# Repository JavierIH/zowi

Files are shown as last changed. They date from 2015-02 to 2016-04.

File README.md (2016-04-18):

# ZOWI

In this repository you will find the source files for the **bq Zowi** robot. If you are missing something, please do not hesitate to [file an issue on github](https://github.com/bq/zowiissues)

En este repositorio se encuentran los ficheros fuente del robot **Zowi de bq**. Si echas en falta algo, no dudes en [rellenar una tarea en github](https://github.com/bq/zowi/issues)

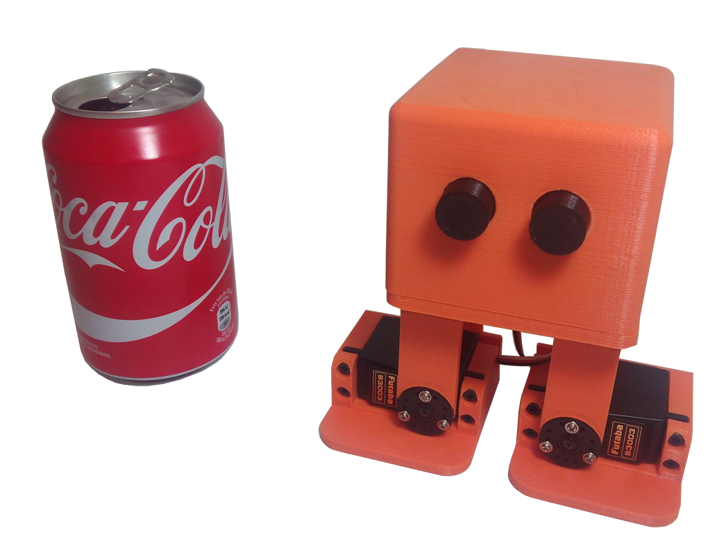
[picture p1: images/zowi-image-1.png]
 

More information in this post in DIWO: [Zowi, introducción a los robots bípedos](http://diwo.bq.com/zowi-introduccion-a-los-robots-bipedos/) (In spanish)

## Designed in Freecad

Zowi is not only an open source robot, but it has also been designed using the open source tool FreeCAD. This way, anyone can open the parts, study them, modify them and distribute the modifications

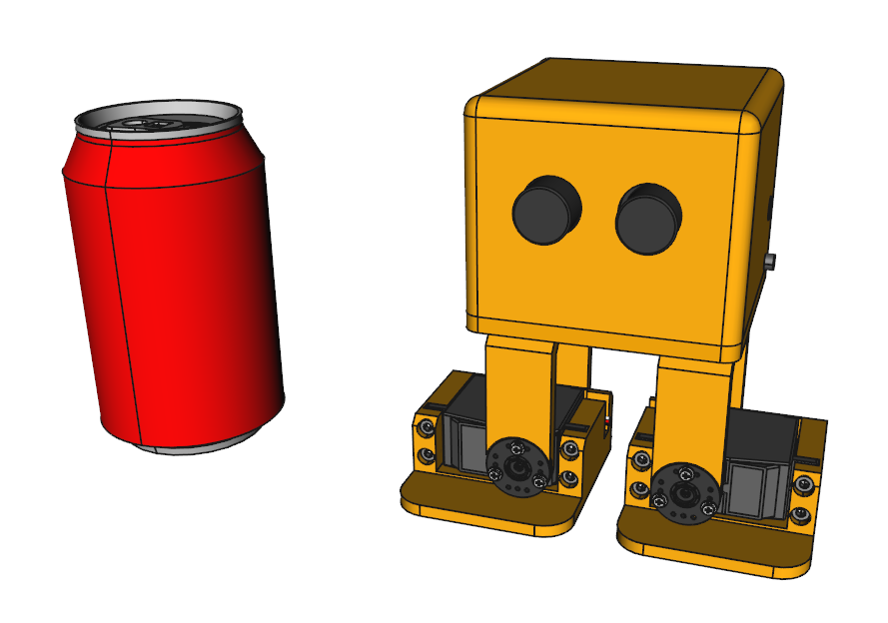
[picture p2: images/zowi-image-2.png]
 

# BOM: Bill of Materials

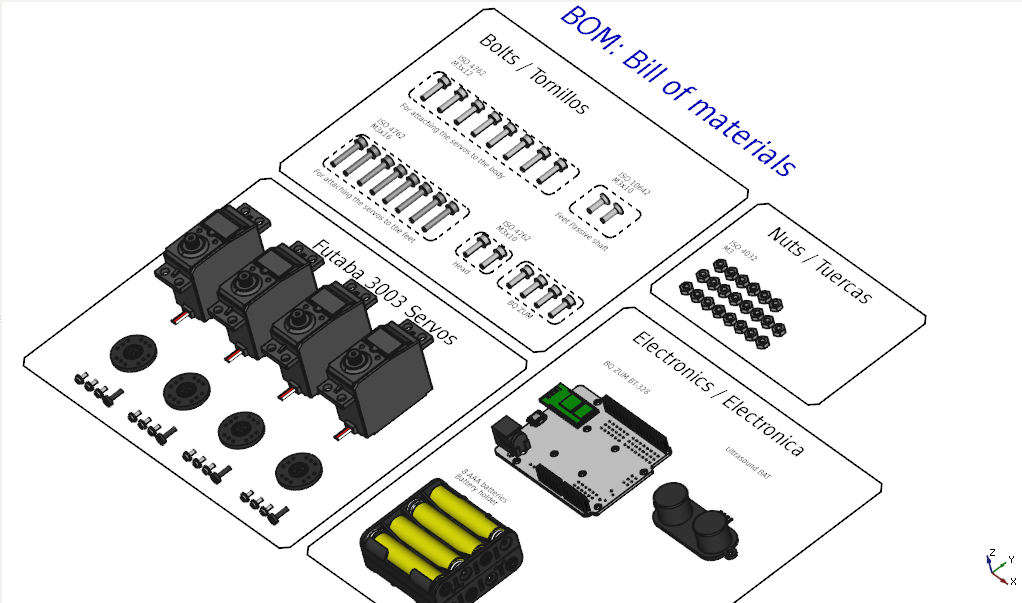
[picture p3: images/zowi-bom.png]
 

* 4 Futaba 3003 servos or compatibles
* 6 M3x10 Bolts (ISO 4762)
* 2 M3x10 Bolts (ISO 10642)
* 8 M3x12 Bolts (ISO 4762)
* 8 M3x16 Bolts (ISO 4762)
* 22 M3 nuts (ISO 4032)
* 1 BQ ZUM BT328 or Arduino
* 4 x 2 AAA Battery holder
* 8 AAA bateries

# License 



This robot is licensed under a [Creative Commons Attribution-ShareAlike 4.0 International License](http://creativecommons.org/licenses/by-sa/4.0/). Please read the LICENSE files for more details.

Este robot tiene una licencia [Creative Commons Attribution-ShareAlike 4.0 International License](http://creativecommons.org/licenses/by-sa/4.0/). Por favor, lea los ficheros LICENSE para más detalles

Original concept by [k120189](http://www.thingiverse.com/k120189/about) on [Thingiverse](http://www.thingiverse.com/thing:43708)

More information: [Zowi CC-BY-SA](http://diwo.bq.com/zowi-cc-by-sa/)

# Other

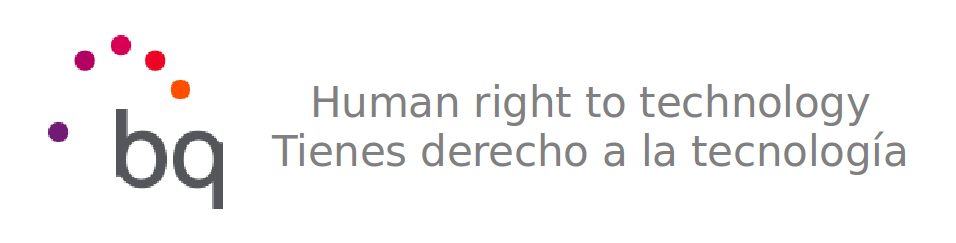
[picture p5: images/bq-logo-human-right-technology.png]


Sponsored by BQ till march 2016

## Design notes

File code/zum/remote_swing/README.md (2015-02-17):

accController -> Protocoder
swing -> Zum (Arduino)

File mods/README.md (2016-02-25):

#Zowi mods

| JIM | Scopum | Micro Raider |
| --- | --- | --- | --- |
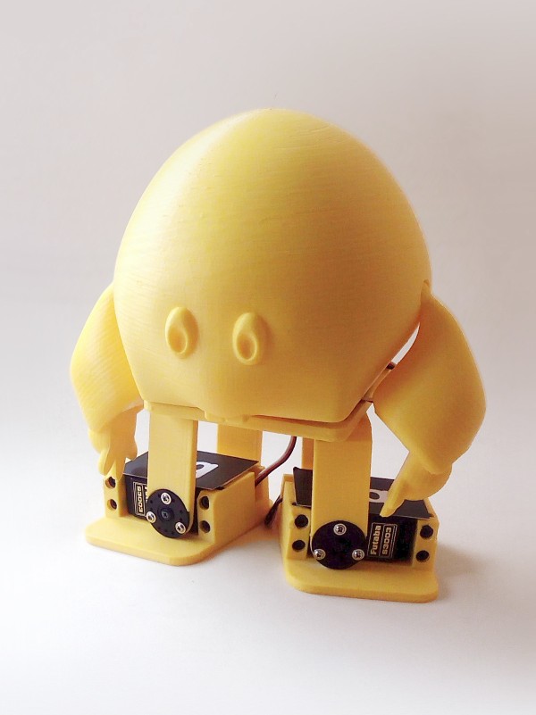
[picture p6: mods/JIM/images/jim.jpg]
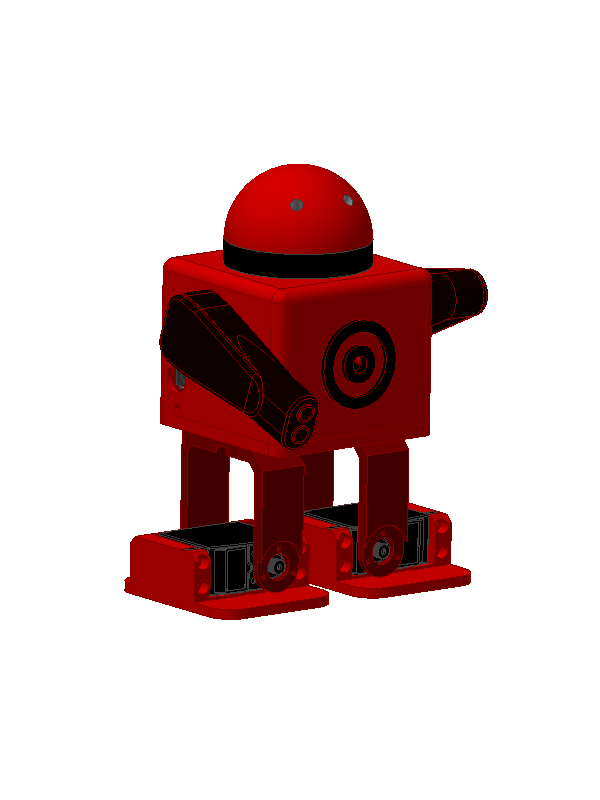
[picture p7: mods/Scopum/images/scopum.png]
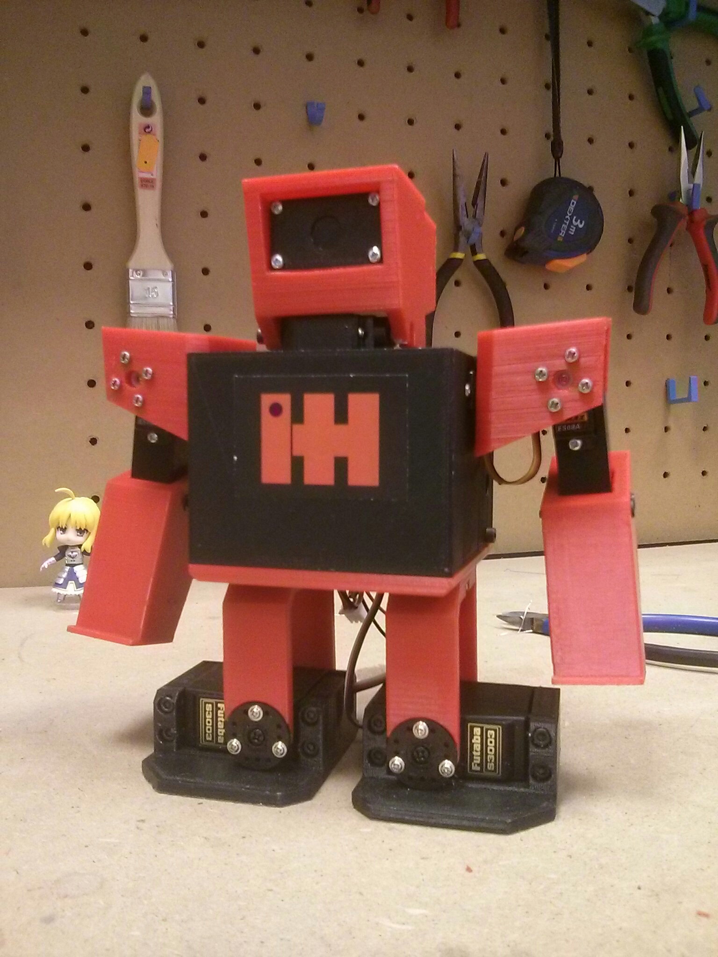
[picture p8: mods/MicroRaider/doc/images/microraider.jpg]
|  |  |  |
| By [Sonia Verdú](http://www.soniaverdu.es/) | By [Macarena González](https://github.com/MacarenaGB)| By  [Javier Isabel](https://github.com/JavierIH)|

| Forge | Zowiquilator | Kobuki |
| --- | --- | --- | --- |
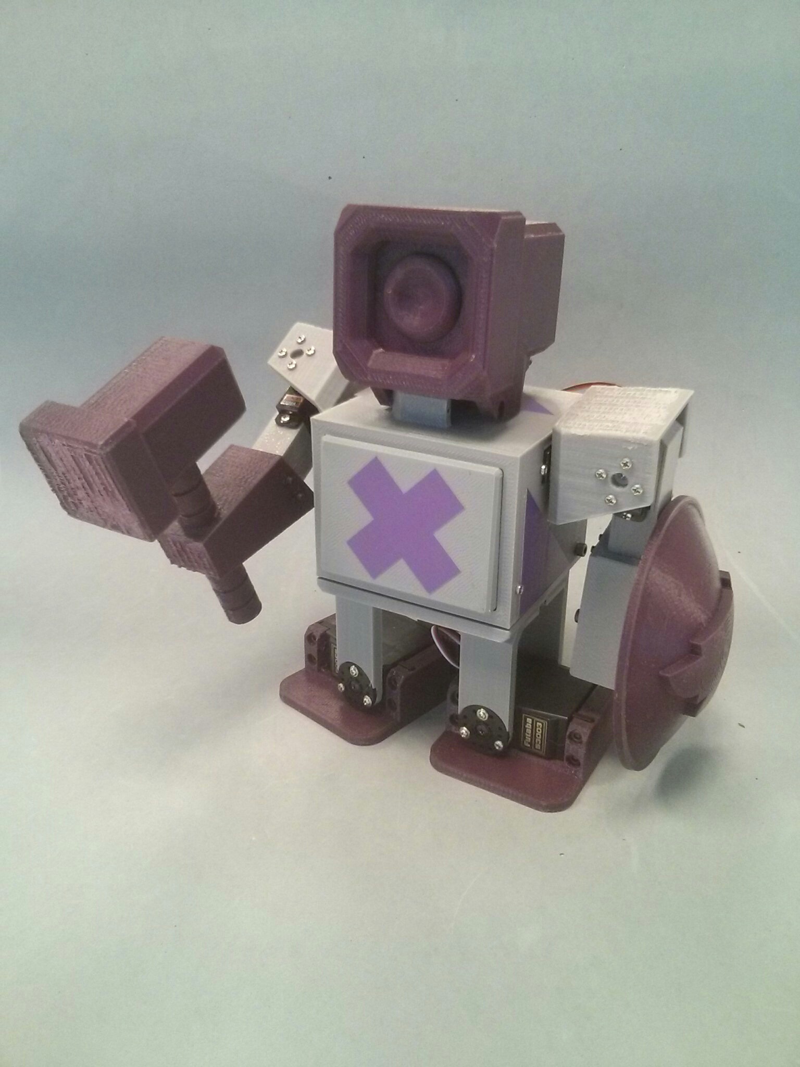
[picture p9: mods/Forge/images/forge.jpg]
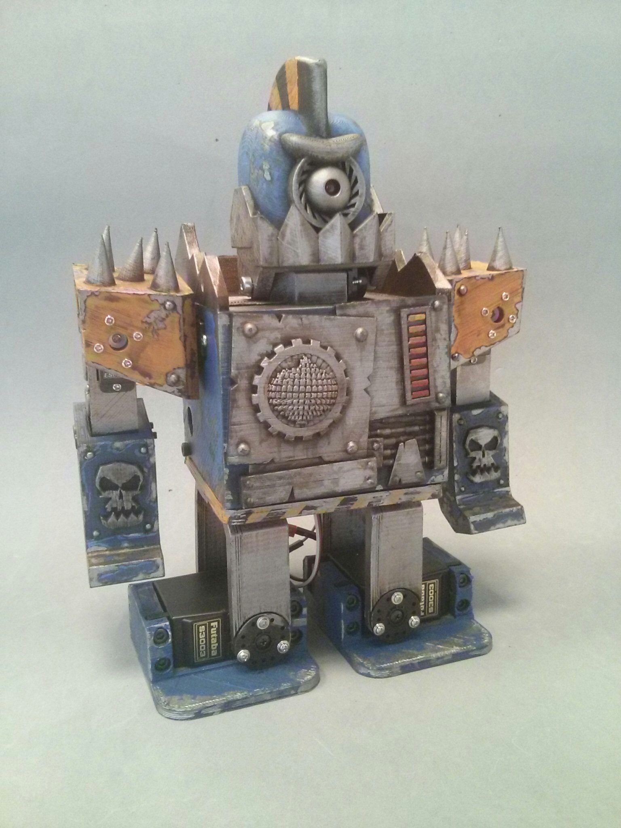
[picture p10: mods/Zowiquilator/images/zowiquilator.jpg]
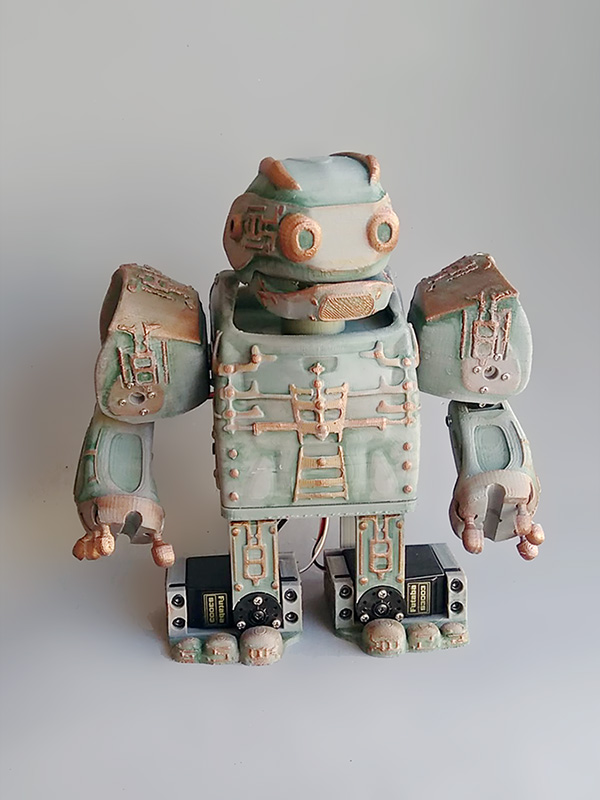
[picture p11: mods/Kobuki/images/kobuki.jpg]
| |  |  |
| By [David Sánchez](https://github.com/davidsanfal) | by [Alberto Arribas](http://www.albertoarribasart.com/)  | By [Sonia Verdú](http://www.soniaverdu.es/) |

| Zowimanoid (template)| IronZowi |  |
| --- | --- | --- | --- |
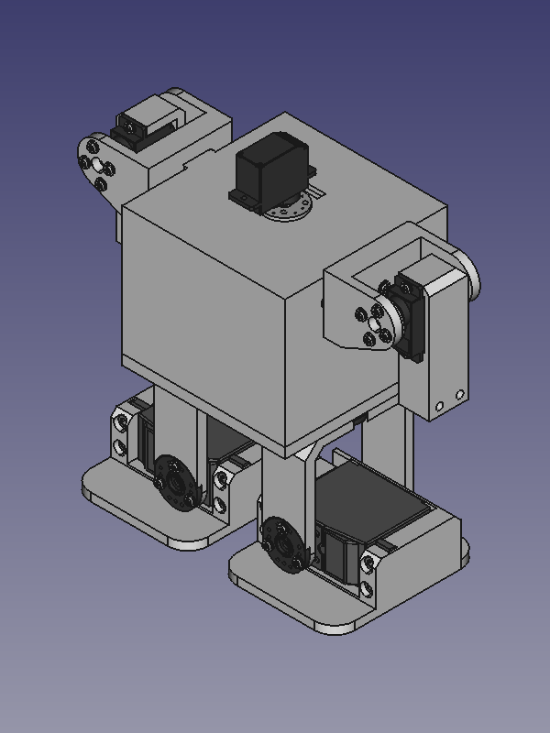
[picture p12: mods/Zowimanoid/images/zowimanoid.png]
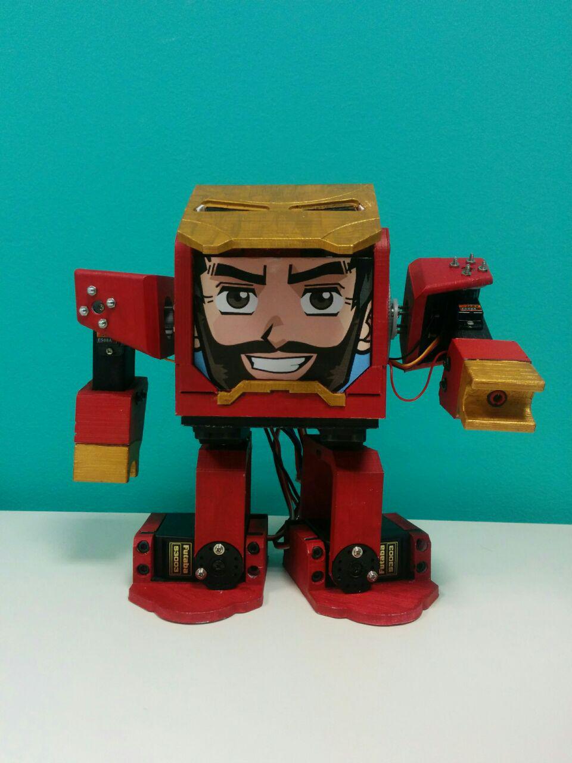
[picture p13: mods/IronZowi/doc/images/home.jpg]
|  | | |
| By  [Javier Isabel](https://github.com/JavierIH) | By  [Gianluca Pugliese](https://github.com/owenlab) | |

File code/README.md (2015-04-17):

La librería de osciladores utilizada en estos programas, puede descargarse desde https://github.com/Obijuan/ArduSnake

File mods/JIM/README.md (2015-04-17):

<p align="center">

</p>
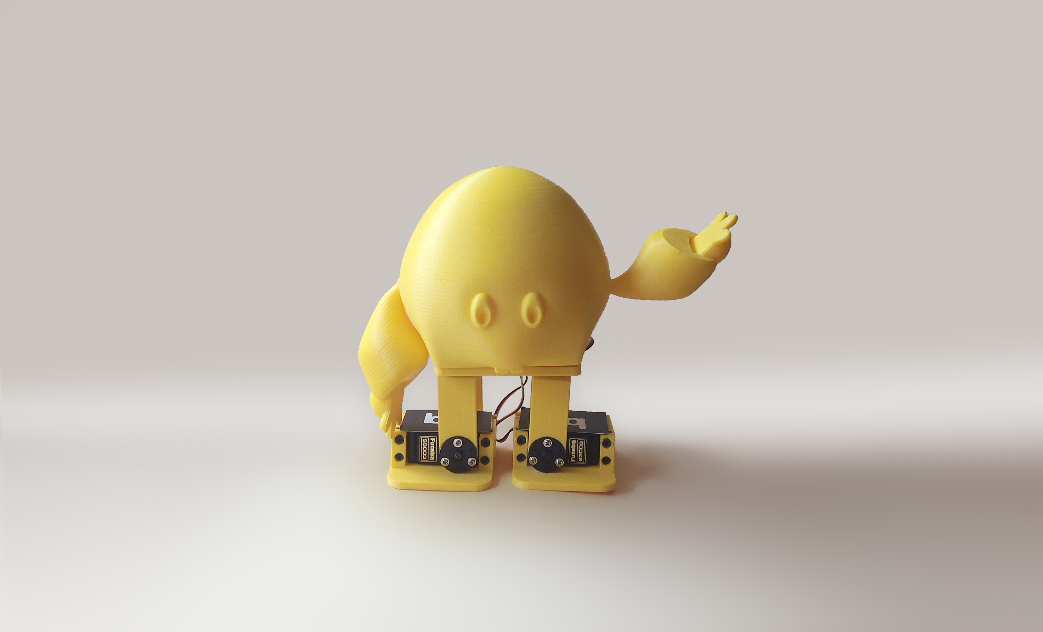
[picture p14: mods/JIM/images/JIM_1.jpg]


# License 



This robot is licensed under a [Creative Commons Attribution-ShareAlike 4.0 International License](http://creativecommons.org/licenses/by-sa/4.0/). Please read the LICENSE files for more details.

Este robot tiene la licencia [Creative Commons Attribution-ShareAlike 4.0 International License](http://creativecommons.org/licenses/by-sa/4.0/). Por favor, lea los ficheros LICENSE para más detalles

# CREDITS

* **Sonia Verdú Calatayud**: Original design

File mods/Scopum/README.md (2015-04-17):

# Scopum

Scopum has been created by [HackLab UPM Bq](http://hacklabupm.bq.com/doku.php?id=start). 
He has been designed in order to have a battle with more Scopums. He has a target in the chest with a receptor fototransistor and a emisor diode in the weapon which is in his arm. Besides, he include a buzzer destinated to make sound when he shoots and when he dies.

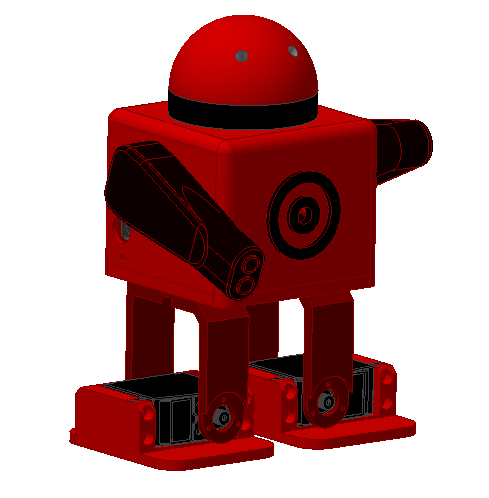
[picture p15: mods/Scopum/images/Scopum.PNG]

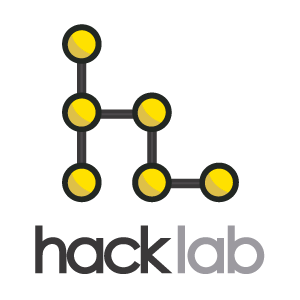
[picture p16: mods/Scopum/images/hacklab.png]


Original concept by [JavierIH](https://github.com/JavierIH) on [Github](https://github.com/bq/zowi)

# License 



This robot is licensed under a [Creative Commons Attribution-ShareAlike 4.0 International License](http://creativecommons.org/licenses/by-sa/4.0/). Please read the LICENSE files for more details.

Este robot tiene la licencia [Creative Commons Attribution-ShareAlike 4.0 International License](http://creativecommons.org/licenses/by-sa/4.0/). Por favor, lea los ficheros LICENSE para más detalles

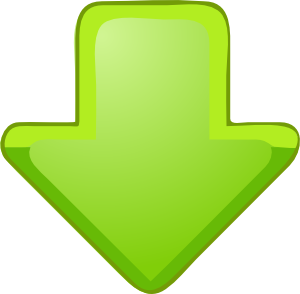
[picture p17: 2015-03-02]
code/protocoder/images/arrow-down-300px.png

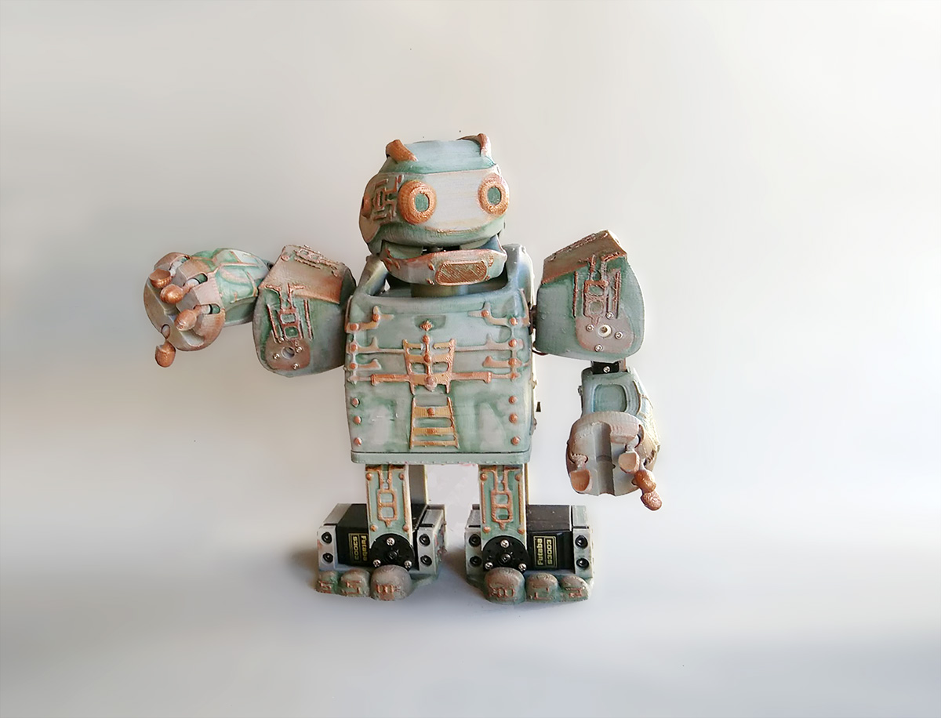
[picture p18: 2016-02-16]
mods/Kobuki/images/kobuki 02.jpg

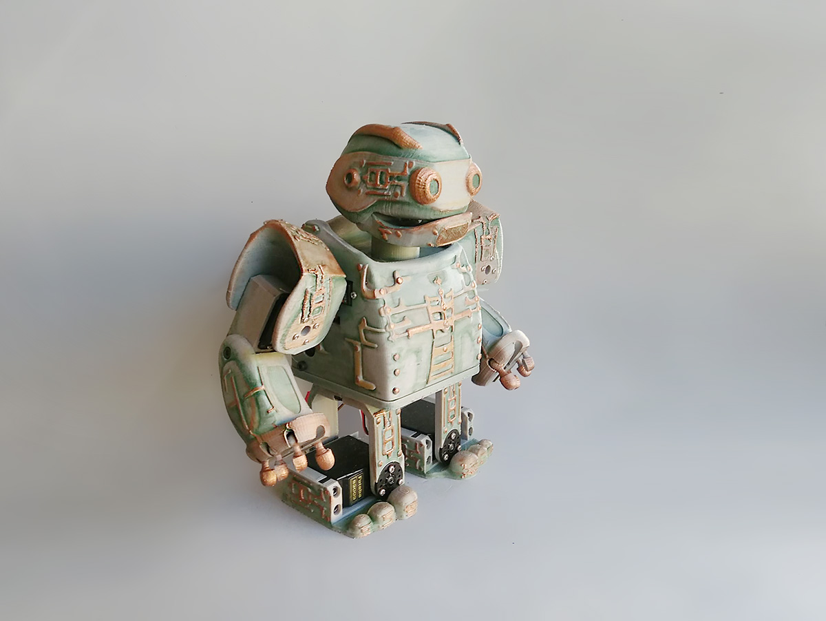
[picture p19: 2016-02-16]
mods/Kobuki/images/kobuki 03.jpg

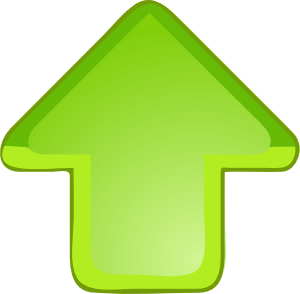
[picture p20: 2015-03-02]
code/protocoder/images/arrow-up.png

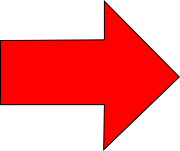
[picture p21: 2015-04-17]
mods/Scopum/code/Protocoder/images/mover_derecha.png

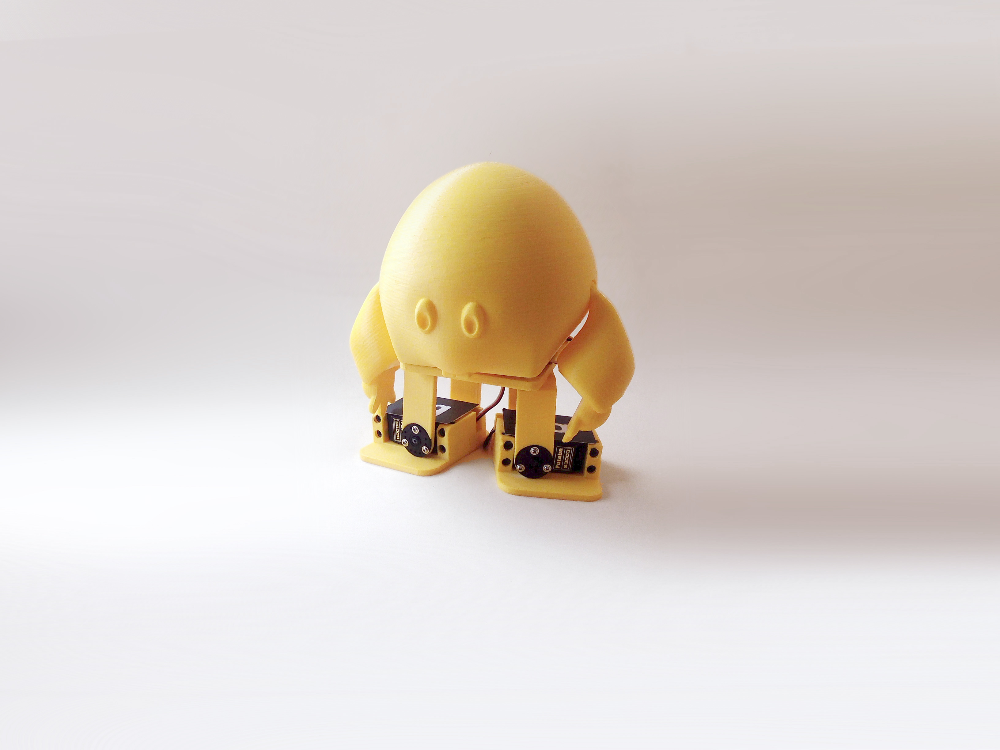
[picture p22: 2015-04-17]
mods/JIM/images/JIM_2.jpg

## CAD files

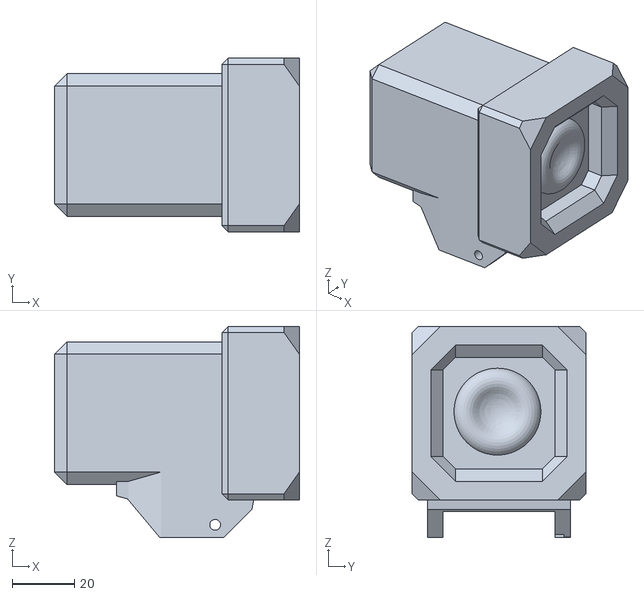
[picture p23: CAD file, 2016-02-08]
mods/Forge/parts/stl/head.stl
79.0 x 56.0 x 68.1

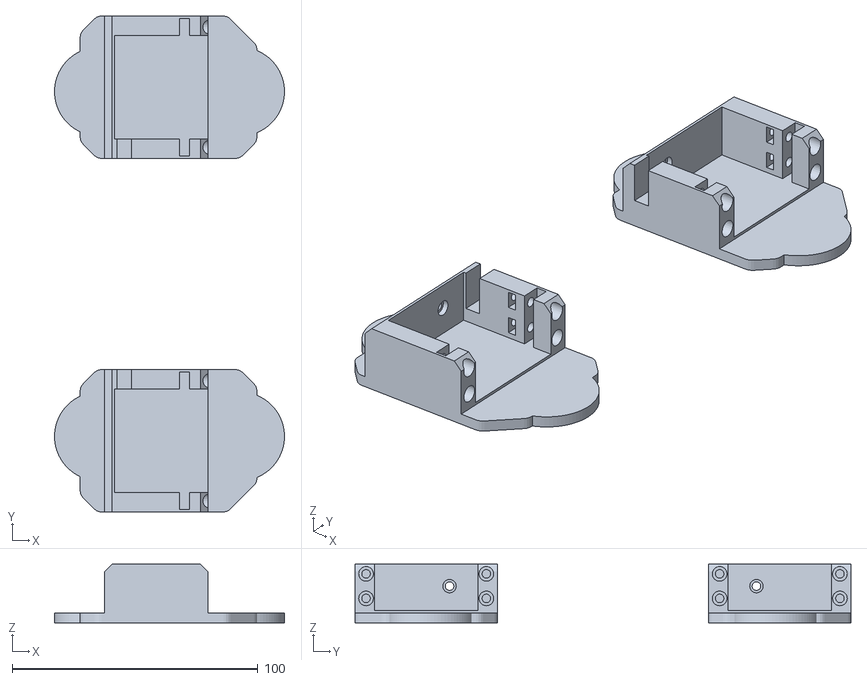
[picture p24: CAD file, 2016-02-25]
mods/IronZowi/parts/stl/feet.stl
93.7 x 202.0 x 24.0

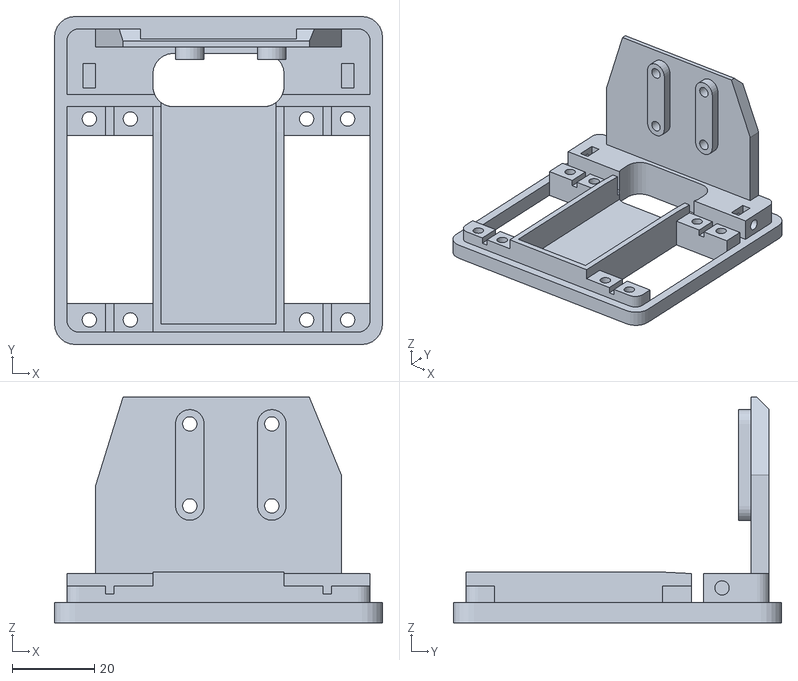
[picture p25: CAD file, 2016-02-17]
mods/Kobuki/parts/stl/base.stl
80.0 x 80.0 x 55.0

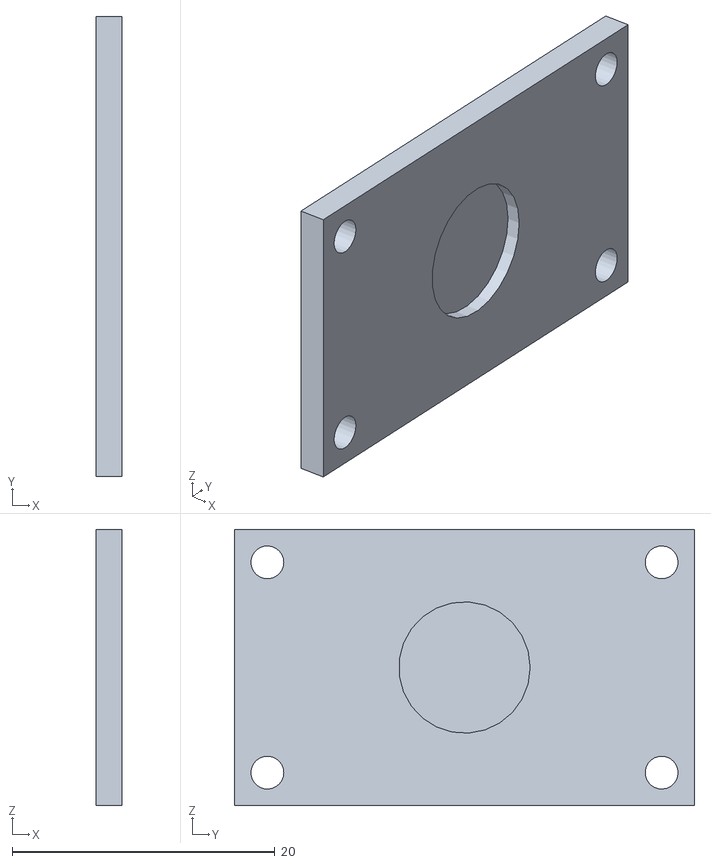
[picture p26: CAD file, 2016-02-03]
mods/MicroRaider/parts/stl/face.stl
2.00 x 35.0 x 21.0

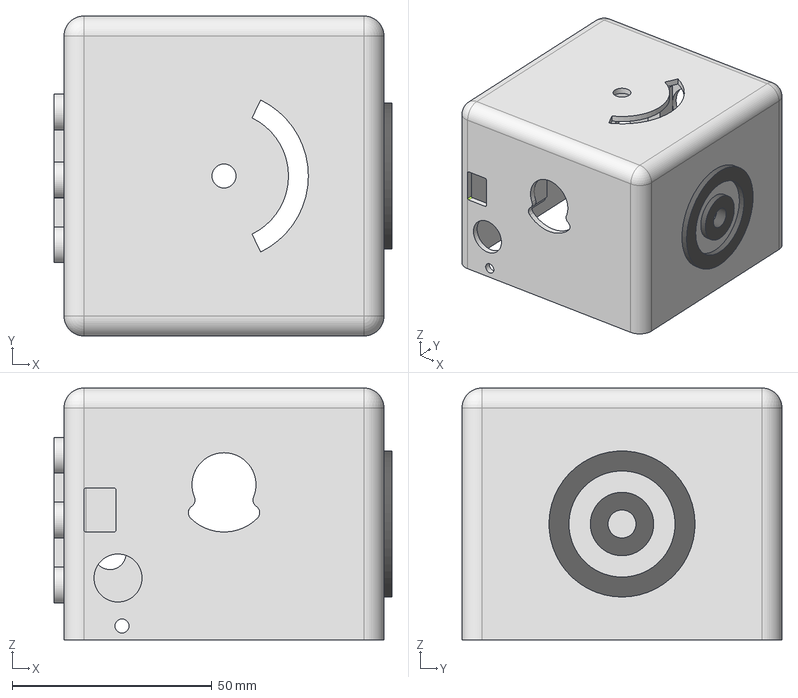
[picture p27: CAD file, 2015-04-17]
mods/Scopum/parts/step/body.step
84.5 x 80.0 x 63.0 mm

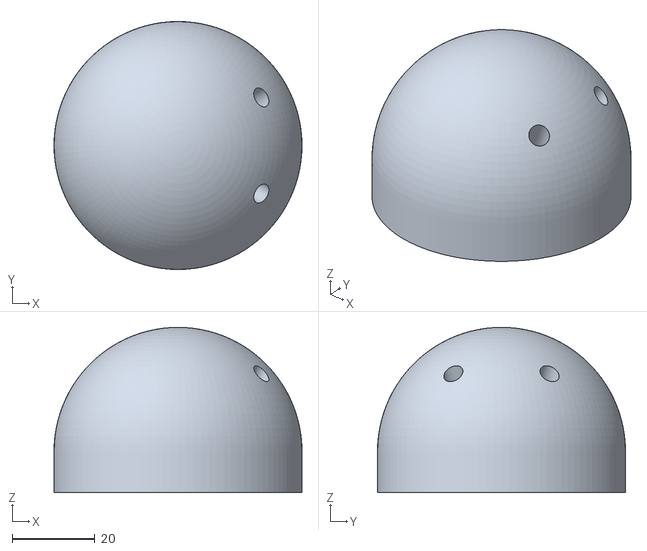
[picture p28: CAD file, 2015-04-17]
mods/Scopum/parts/stl/head.stl
60.0 x 60.0 x 40.0

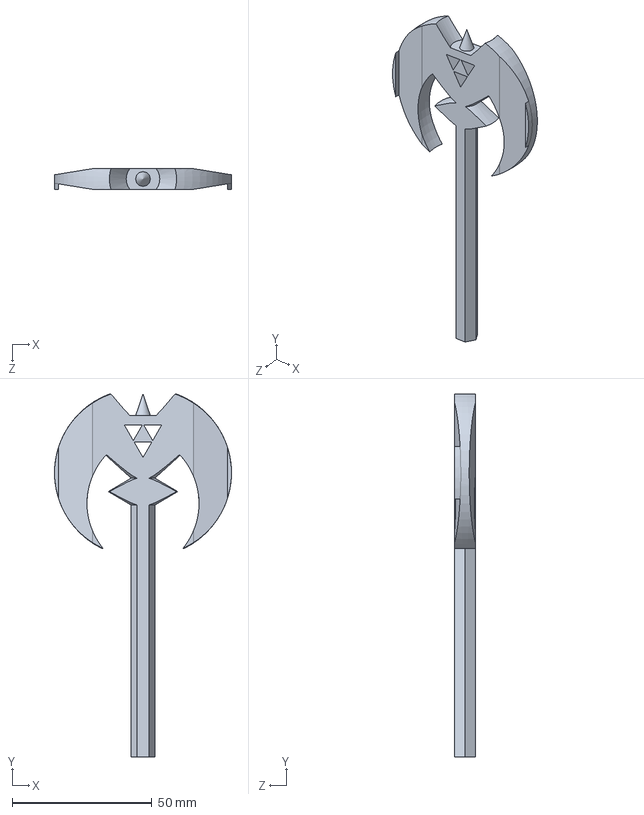
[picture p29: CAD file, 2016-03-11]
mods/Zowarrior/parts/solid/axe.SLDPRT
63.2 x 129.6 x 7.40 mm

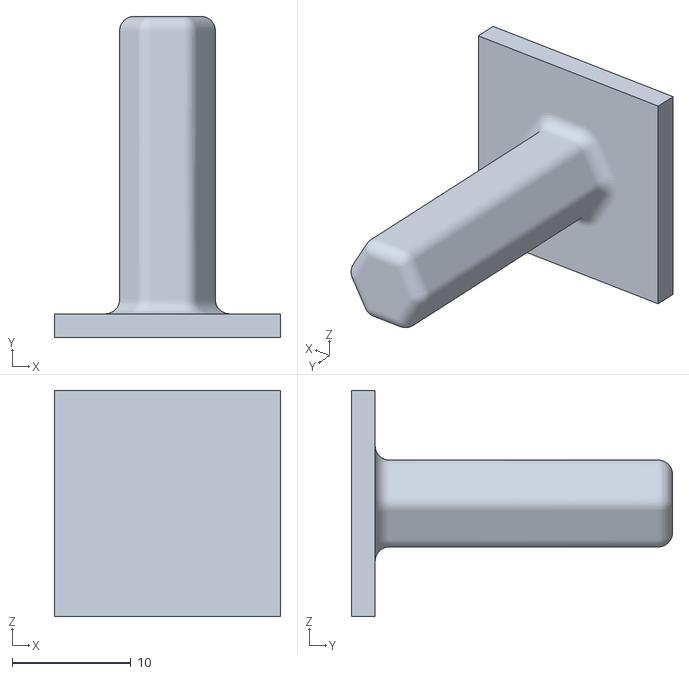
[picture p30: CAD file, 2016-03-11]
mods/Zowarrior/parts/stl/shield_hand.STL
19.0 x 27.0 x 19.0

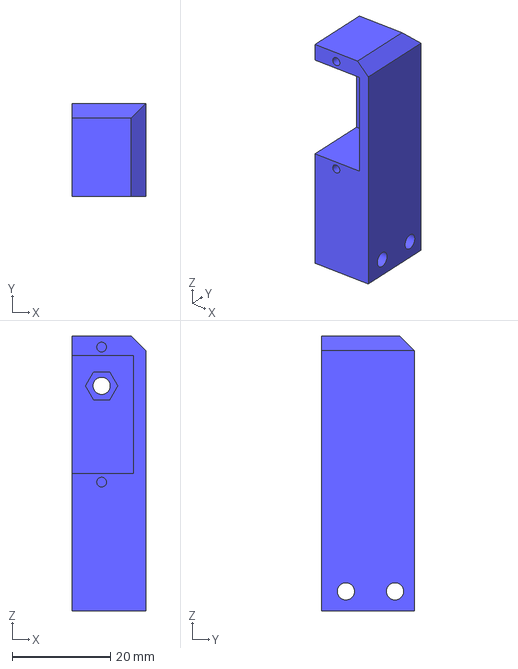
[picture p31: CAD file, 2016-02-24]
mods/Zowimanoid/parts/step/leftArm.step
15.0 x 19.0 x 56.0 mm

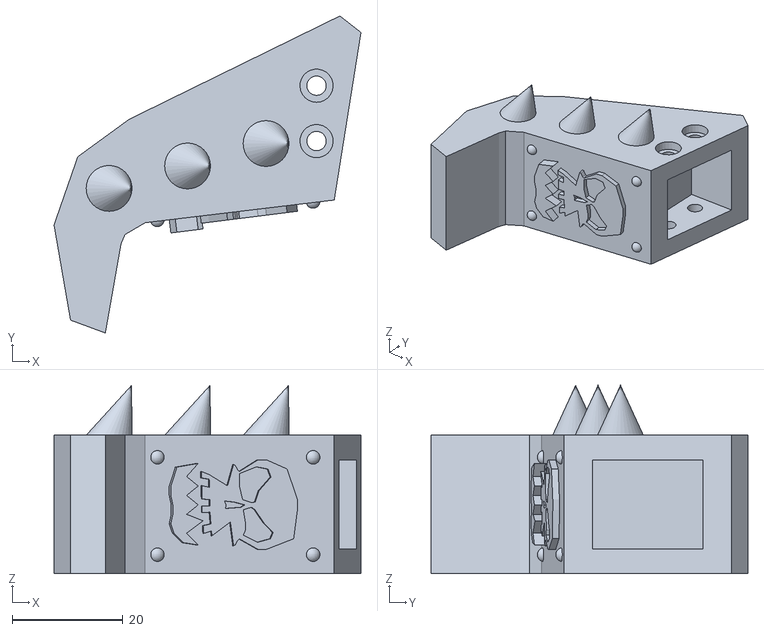
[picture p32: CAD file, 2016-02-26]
mods/Zowiquilator/parts/stl/PunoD_fixed.stl
55.4 x 57.3 x 34.0

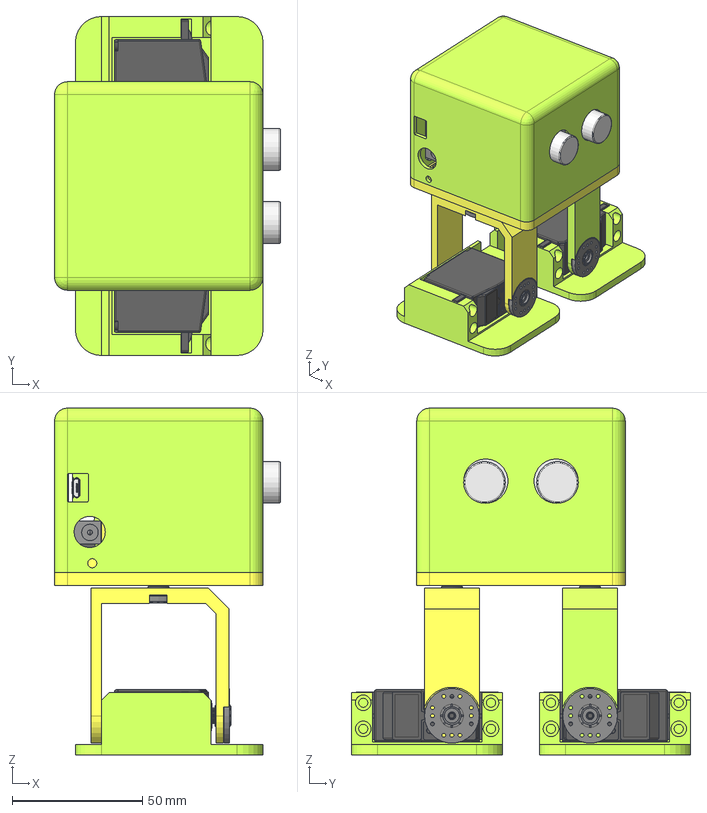
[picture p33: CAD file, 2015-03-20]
parts/freecad/zob.fcstd
86.7 x 130.0 x 133.0 mm
J1
J2
J4
J16
PCB
J010
U1
J8
Servo-D1
Servo-D2
Servo-D1 (Mirror #1)
Servo-D2 (Mirror #2)
horn
horn001
horn (Mirror #4)
horn001 (Mirror #5)
pies001
pies
pataD
pataI
peterpilas
Ultrasonido_BAT
chasis

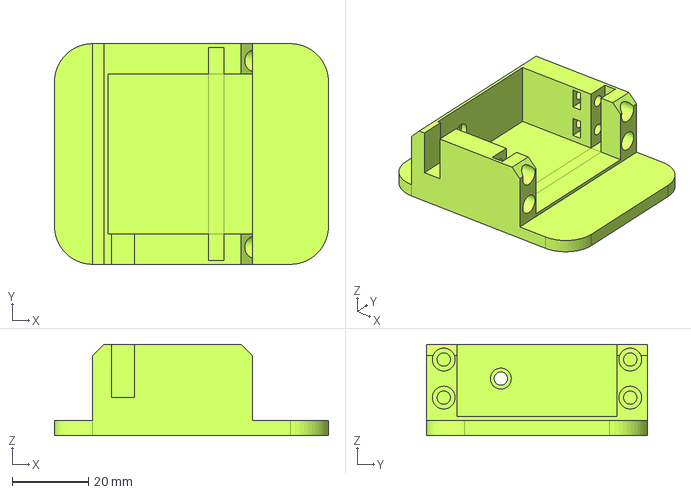
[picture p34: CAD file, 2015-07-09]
parts/step/footL.step
72.0 x 58.0 x 24.0 mm

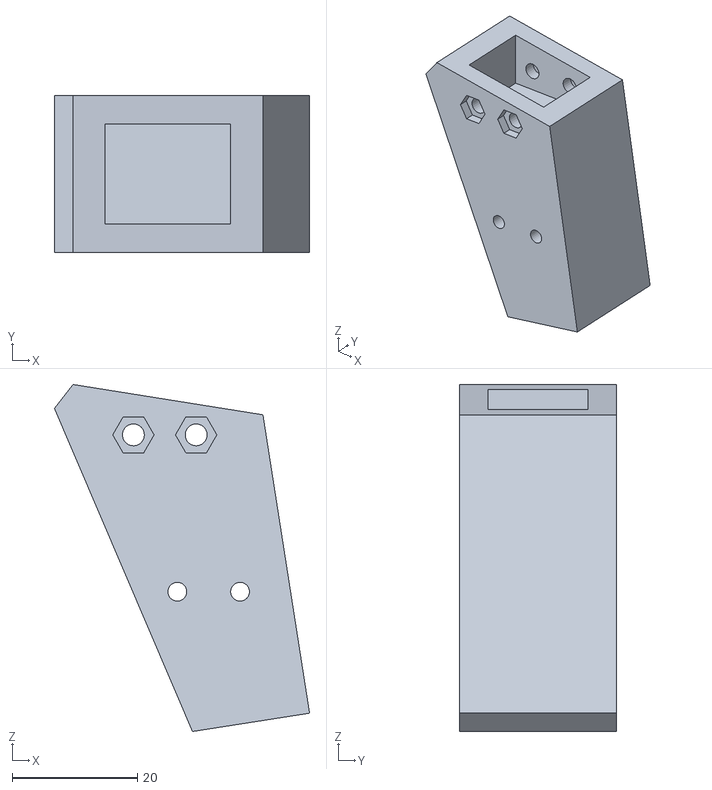
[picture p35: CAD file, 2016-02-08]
mods/Forge/parts/stl/handL.stl
40.7 x 25.0 x 55.3

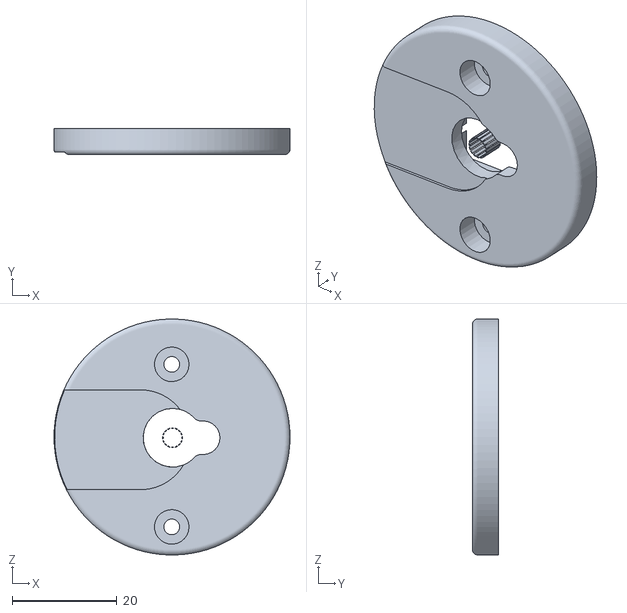
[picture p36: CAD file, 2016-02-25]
mods/IronZowi/parts/stl/ear2.stl
45.0 x 5.00 x 45.0

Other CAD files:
mods/Kobuki/parts/stl/jaw.stl
mods/MicroRaider/parts/stl/faceB.stl
mods/Scopum/parts/step/chassis.step
mods/Scopum/parts/stl/ZUM_BT_328.stl
mods/Forge/parts/stl/armL.stl
mods/Forge/parts/stl/armR.stl
mods/Forge/parts/stl/body.stl
mods/Forge/parts/stl/body_button.stl
mods/Forge/parts/stl/chassis.stl
mods/Forge/parts/stl/footL.stl
mods/Forge/parts/stl/footR.stl
mods/Forge/parts/stl/handR.stl
mods/Forge/parts/stl/leg.stl
mods/Forge/parts/stl/shield.stl
mods/Forge/parts/stl/shoulderL.stl
mods/Forge/parts/stl/shoulderR.stl
mods/IronZowi/parts/stl/arms.stl
mods/IronZowi/parts/stl/base.stl
mods/IronZowi/parts/stl/ear1.stl
mods/IronZowi/parts/stl/hands.stl
mods/IronZowi/parts/stl/head.stl
mods/IronZowi/parts/stl/mask.stl
mods/IronZowi/parts/stl/shoulders.stl
mods/IronZowi/parts/stl/top.stl
mods/Kobuki/parts/stl/head.stl
mods/Kobuki/parts/stl/humerus right.stl
mods/Kobuki/parts/stl/left foot.stl
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

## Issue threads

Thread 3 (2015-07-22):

Refactorization of zowi parts

Obijuan, 2015-07-22:
Zowi parts can be implemented easily using sketches and clones. It will make it easier for the people to change the parts and create derivative designs.

Obijuan, 2015-07-22:
The leg part has been already refactored. I am working in my fork. When every part is finished, printed and tested I will merge into zowi's master

Leg parts has not been printed nor tested yet

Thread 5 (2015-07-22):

[Improvement] Improve how the Futaba 3003 fits in the foot

Obijuan, 2015-07-22:
The Futaba 3003 servo does not fit well on the foot. It have to be pressed hard. It is also difficult to remove.  It would be better improve this part, so that the servos can be attached and detached easily

cparrapa, 2016-02-14:
Had same issue also the pin in the back limit the use of one kind of m3 screw.

arodriguezf, 2016-03-11:
I had the same problem

jabyrd3, 2017-12-09:
I had to file down a small fin on the plastic support tabs to get the futaba servo to fit at all. Pressing hard didn't even do the trick.

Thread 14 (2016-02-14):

Como evadir obstaculos con Zowi?

cparrapa, 2016-02-14:
Hola de antemano gracias por los modelos 3d y las librerias para Zowi, pero con ninguno de los códigos en podido hacer que Zowi evada obstáculos con el ultrasonido, alguna sugerencia?

cparrapa, 2016-02-19:
Any quick code to make Zowi avoid obstacles?

Anadeprado, 2016-02-19:
Debes tener tu sensorUS conectado a pines:  _trigger_pin_, _echo_pin_

Dentro del bucle principal, podrías medir distancia cada vez que Zowi de un pasito:
```
   zowi.walk(1,1000,1);                  //Zowi da un paso

   int distance = getDistance();         //Medimos distancia

        if(distance<15){                 //Si hay algo a 15 centímetros...
                //...Obstacle Detected
        }else{
                //...No Obstacle
        }

```

Funciones para medir distancia en centímetros con el sensorUS:

```
long TP_init(){

  digitalWrite(trigger_pin, LOW);
  delayMicroseconds(2);
  digitalWrite(trigger_pin, HIGH);
  delayMicroseconds(10);
  digitalWrite(trigger_pin, LOW);
  long microseconds = pulseIn(echo_pin ,HIGH,40000);
  return microseconds;

}

long getDistance(){

     long microseconds = TP_init();
     long distance;
     distance = microseconds/29/2;
     if (distance == 0){
             distance = 999;
     }
     return distance;
}
```

cparrapa, 2016-02-20:
@Anadeprado funciono!, mil gracias, luego de una semana intentando era así de simple, al parecer las librerías de aquí** bq / zowiLibs** no funcionan con los mismos códigos que las de este repositorio (**bqlabs/zowi**); en uno llaman Zowi zowi y en otro z, y el zowi.h es diferente, y la final para que funcionara tuve que utilizar el setup de **bq/bitbloqLibs** como en un tutorial de @agomezgar, el código final fue el siguiente:
```
#include <BitbloqZowi.h>
#include <BitbloqUS.h>
#include <BitbloqBatteryReader.h>
#include <BitbloqLedMatrix.h>
#include <Servo.h>
#include <BitbloqOscillator.h>
#include <EEPROM.h>
#define PIN_RR 5
#define PIN_RL 4
#define PIN_YR 3
#define PIN_YL 2
#define trigger_pin 8
#define echo_pin 9
#define TRIM_RR   0
#define TRIM_RL   -5
#define TRIM_YR   0
#define TRIM_YL  -5

Zowi zowi;
void setup()
{
  zowi.init();
    zowi.init(PIN_YL, PIN_YR, PIN_RL, PIN_RR);
    zowi.setTrims(TRIM_YL, TRIM_YR, TRIM_RL, TRIM_RR);
}
void loop()
{
  zowi.home();
  zowi.sing(S_happy);
           zowi.walk(1,1000,1);         //Zowi da un paso

   int distance = getDistance();         //Medimos distancia
        if(distance<15){                 //Si hay algo a 15 centímetros...
              zowi.walk(4, LOW_SPEED, BACKWARD);  //...Obstacle Detected
    zowi.sing(S_confused);
      }else{
                 //...No Obstacle
        }
}
long TP_init(){
  digitalWrite(trigger_pin, LOW);
  delayMicroseconds(2);
  digitalWrite(trigger_pin, HIGH);
  delayMicroseconds(10);
  digitalWrite(trigger_pin, LOW);
  long microseconds = pulseIn(echo_pin ,HIGH,40000);
  return microseconds;
}

long getDistance(){
     long microseconds = TP_init();
     long distance;
     distance = microseconds/29/2;
     if (distance == 0){
             distance = 999;
     }
     return distance;
}
```

Closed 2016-02-20.

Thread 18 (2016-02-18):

Zowimaoid neutral CAD files please

cparrapa, 2016-02-18:
Hi @JavierIH can you please provide .stp or .igs neutral CAD files so i can work on top of that in other 3d software aside from freeCAD?, zowi/mods/Zowimaoid/

JavierIH, 2016-02-18:
Hi, thank you for your feedback. I have generated steps, obj and stl files. They can be found here: https://github.com/bqlabs/zowi/tree/master/mods/Zowimanoid/parts

cparrapa, 2016-02-19:
Perfect thanks for the quick response.

Closed 2016-02-19.

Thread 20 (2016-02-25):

Puño derecho de Zowiquilator

SummeiL, 2016-02-25:
Hola compañeros,

el puño derecho del mod Zowiquilator creo que es erróneo, podéis subir la pieza correcta? Solo me falta esa para montarlo :)

Gracias!

JavierIH, 2016-02-26:
Hola,
En efecto, el archivo estaba equivocado. Acabo de subir la pieza correcta.

Gracias por el aviso :)

Closed 2016-02-26.

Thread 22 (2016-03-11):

Problem with arduino board

arodriguezf, 2016-03-11:
When I upload the code to an arduino board with a speaker connected to it, it sounds like an constant alarm, sometimes when I reboot the board it starts ok and do the programation, but when I get the alarm it only fires the alarm and don´t do anything. I tested in 2 boards with the same result, can you help me?

cparrapa, 2016-03-14:
Which code and libraries are you using?, double check the connection of the servos. Is it Arduino UNO?

arodriguezf, 2016-03-15:
I'm using the libraries from https://github.com/bq/zowiLibs and code fromhttps://github.com/bq/zowiLibs/tree/master/code%20.ino/ZOWI_BASE_v2 but I think I tried with other codes and I get the same result.
I will check the connection of the servos but they are working when the alarm is not makeing sound.
Yes, is with arduino one.

cparrapa, 2016-03-15:
Try this library https://github.com/bqlabs/zowi/tree/master/code/zum/libraries with this code https://github.com/agomezgar/tutoriales/tree/master/tutorialZowi1/zowi_walk_ino

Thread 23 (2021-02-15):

Problemas compilando

lobras77, 2021-02-15:
Hola. Hace un par de semanas llegó a mis manos una impresora 3d e investigando llegué a Bobwi. He impreso las piezas e iba a montarlo con un Arduino Nano.

He probado todos los códigos de la web de Galileo, el tuyo de Zowi y todos me dan errores en la compilación. Me podrías echar una mano? Te lo agradezco de antemano.

Un saludo

lobras77, 2021-02-15:
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
Esto es lo que me sale al copiar y pegar el código y compilarlo.

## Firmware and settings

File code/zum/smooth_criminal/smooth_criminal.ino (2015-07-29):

#include <Servo.h>
#include <Oscillator.h>
#include <EEPROM.h>

#define N_SERVOS 4

//-- Have a look at the file zowi_walk_ino.ino for the documentation on how
//-- the servos are attached

#define EEPROM_TRIM 0 //Activar para coger los datos de calibracin desde la memoria interna

#define TRIM_RR -7
#define TRIM_RL -2
#define TRIM_YR  0
#define TRIM_YL -14

#define PIN_RR 5
#define PIN_RL 4
#define PIN_YR 3
#define PIN_YL 2

#define INTERVALTIME 10.0 

Oscillator servo[N_SERVOS];

void goingUp(int tempo);
void drunk (int tempo);
void noGravity(int tempo);
void kickLeft(int tempo);
void kickRight(int tempo);
void run(int steps, int T=500);
void walk(int steps, int T=1000);
void backyard(int steps, int T=3000);
void backyardSlow(int steps, int T=5000);
void turnLeft(int steps, int T=3000);
void turnRight(int steps, int T=3000);
void moonWalkLeft(int steps, int T=1000);
void moonWalkRight(int steps, int T=1000);
void crusaito(int steps, int T=1000);
void swing(int steps, int T=1000);
void upDown(int steps, int T=1000);
void flapping(int steps, int T=1000);

void setup()
{
  Serial.begin(19200);
  
  servo[0].attach(PIN_RR);
  servo[1].attach(PIN_RL);
  servo[2].attach(PIN_YR);
  servo[3].attach(PIN_YL);
  
  //EEPROM.write(0,TRIM_RR);
  //EEPROM.write(1,TRIM_RL);
  //EEPROM.write(2,TRIM_YR);
  //EEPROM.write(3,TRIM_YL);
  
  int trim;
  
  if(EEPROM_TRIM){
    for(int x=0;x<4;x++){
      trim=EEPROM.read(x);
      if(trim>128)trim=trim-256;
      Serial.print("TRIM ");
      Serial.print(x);
      Serial.print(" en ");
      Serial.println(trim);
      servo[x].SetTrim(trim);
    }
  }
  else{
    servo[0].SetTrim(TRIM_RR);
    servo[1].SetTrim(TRIM_RL);
    servo[2].SetTrim(TRIM_YR);
    servo[3].SetTrim(TRIM_YL);
  }
  
  for(int i=0;i<4;i++) servo[i].SetPosition(90);
}

// TEMPO: 121 BPM
int t=495;
double pause=0;

void loop()
{
 // if(Serial.available()){
  //  char init = Serial.read();
   // if (init=='X'){
   //   delay(4000); //3000 - 4500
   
dance();


//for(int i=0;i<4;i++) servo[i].SetPosition(90);

      
          for(int i=0;i<4;i++) servo[i].SetPosition(90);
   // }
 // }
}

void dance(){
  primera_parte();
  segunda_parte();
  moonWalkLeft(4,t*2);
  moonWalkRight(4,t*2);
  moonWalkLeft(4,t*2);
  moonWalkRight(4,t*2);
  primera_parte(); 
  crusaito(1,t*8);
  crusaito(1,t*7);

  for (int i=0; i<16; i++){
    flapping(1,t/4);
    delay(3*t/4);
  }
 
  moonWalkRight(4,t*2);
  moonWalkLeft(4,t*2);
  moonWalkRight(4,t*2);
  moonWalkLeft(4,t*2);

  drunk(t*4);
  drunk(t*4);
  drunk(t*4);
  drunk(t*4);
  kickLeft(t);
  kickRight(t);
  drunk(t*8);
  drunk(t*4);
  drunk(t/2);
  delay(t*4); 

  drunk(t/2);

  delay(t*4); 
  walk(2,t*2);
  backyard(2,t*2);
  goingUp(t*2);
  goingUp(t*1);
  noGravity(t*2);
  crusaito(1,t*2);
  crusaito(1,t*8);
  crusaito(1,t*2);
  crusaito(1,t*8);
  crusaito(1,t*2);
  crusaito(1,t*3);

  delay(t);
  primera_parte();
    for (int i=0; i<32; i++){
    flapping(1,t/2);
    delay(t/2);
  }
  
  for(int i=0;i<4;i++) servo[i].SetPosition(90);
}




////////////////////////////////////////////////////////////////////////////////////////
//////////////////////////////////FUNCIONES DE CONTROL//////////////////////////////////
////////////////////////////////////////////////////////////////////////////////////////

void oscillate(int A[N_SERVOS], int O[N_SERVOS], int T, double phase_diff[N_SERVOS]){
  for (int i=0; i<4; i++) {
    servo[i].SetO(O[i]);
    servo[i].SetA(A[i]);
    servo[i].SetT(T);
    servo[i].SetPh(phase_diff[i]);
  }
  double ref=millis();
   for (double x=ref; x<T+ref; x=millis()){
     for (int i=0; i<4; i++){
        servo[i].refresh();
     }
  }
}

unsigned long final_time;
unsigned long interval_time;
int oneTime;
int iteration;
float increment[N_SERVOS]; 
int oldPosition[]={90,90,90,90};

void moveNServos(int time, int  newPosition[]){
  for(int i=0;i<N_SERVOS;i++)	increment[i] = ((newPosition[i])-oldPosition[i])/(time/INTERVALTIME);
  
  final_time =  millis() + time; 
  
  iteration = 1; 
  while(millis() < final_time){ //Javi del futuro cambia esto  
      interval_time = millis()+INTERVALTIME;  
      
      oneTime=0;      
      while(millis()<interval_time){	  
          if(oneTime<1){ 
              for(int i=0;i<N_SERVOS;i++){
                  servo[i].SetPosition(oldPosition[i] + (iteration * increment[i]));
              }			
              iteration++;
              oneTime++;
          }
      }     
  }   

  for(int i=0;i<N_SERVOS;i++){	
    oldPosition[i] = newPosition[i];
  }   
}


//////////////////////////////////////////////////////////////////////////////
////////////////////////////////PASOS DE BAILE////////////////////////////////
//////////////////////////////////////////////////////////////////////////////

void goingUp(int tempo){
  
      pause=millis();
      for(int i=0;i<4;i++) servo[i].SetPosition(90);
      delay(tempo);
      servo[0].SetPosition(80);
      servo[1].SetPosition(100);
      delay(tempo);
      servo[0].SetPosition(70);
      servo[1].SetPosition(110);
      delay(tempo);
      servo[0].SetPosition(60);
      servo[1].SetPosition(120);
      delay(tempo);
      servo[0].SetPosition(50);
      servo[1].SetPosition(130);
      delay(tempo);
      servo[0].SetPosition(40);
      servo[1].SetPosition(140);
      delay(tempo);
      servo[0].SetPosition(30);
      servo[1].SetPosition(150);
      delay(tempo);
      servo[0].SetPosition(20);
      servo[1].SetPosition(160);
      delay(tempo);
      
      while(millis()<pause+8*t);

}

void primera_parte(){
  
  int move1[4] = {60,120,90,90};
  int move2[4] = {90,90,90,90};
  int move3[4] = {40,140,90,90};
  
  for(int x=0; x<3; x++){
    for(int i=0; i<3; i++){
      lateral_fuerte(1,t/2);
      lateral_fuerte(0,t/4);
      lateral_fuerte(1,t/4);
      delay(t);
    }
  
    pause=millis();
    for(int i=0;i<4;i++) servo[i].SetPosition(90);
    moveNServos(t*0.4,move1);
    moveNServos(t*0.4,move2);
    while(millis()<(pause+t*2));
  }
  
  for(int i=0; i<2; i++){
    lateral_fuerte(1,t/2);
    lateral_fuerte(0,t/4);
    lateral_fuerte(1,t/4);
    delay(t);
  }
    
  pause=millis();
  for(int i=0;i<4;i++) servo[i].SetPosition(90);
  crusaito(1,t*1.4);
  moveNServos(t*1,move3);
  for(int i=0;i<4;i++) servo[i].SetPosition(90);
  while(millis()<(pause+t*4));
}

void segunda_parte(){
  
  int move1[4] = {90,90,80,100};
  int move2[4] = {90,90,100,80};
  int move3[4] = {90,90,80,100};
  int move4[4] = {90,90,100,80};
    
  int move5[4] = {40,140,80,100};
  int move6[4] = {40,140,100,80};
  int move7[4] = {90,90,80,100};
  int move8[4] = {90,90,100,80};
       
  int move9[4] = {40,140,80,100};
  int move10[4] = {40,140,100,80};
  int move11[4] = {90,90,80,100};
  int move12[4] = {90,90,100,80};
  
  for(int x=0; x<7; x++){ 
    for(int i=0; i<3; i++){
      pause=millis();
      moveNServos(t*0.15,move1);
      moveNServos(t*0.15,move2);
      moveNServos(t*0.15,move3);
      moveNServos(t*0.15,move4);
      while(millis()<(pause+t));
    }
    pause=millis();
    moveNServos(t*0.15,move5);
    moveNServos(t*0.15,move6);
    moveNServos(t*0.15,move7);
    moveNServos(t*0.15,move8);
    while(millis()<(pause+t));
  }
 
  for(int i=0; i<3; i++){
    pause=millis();
    moveNServos(t*0.15,move9);
    moveNServos(t*0.15,move10);
    moveNServos(t*0.15,move11);
    moveNServos(t*0.15,move12);
    while(millis()<(pause+t));
  }
}

void lateral_fuerte(boolean side, int tempo){
  
  for(int i=0;i<4;i++) servo[i].SetPosition(90);
  if (side) servo[0].SetPosition(40);
  else servo[1].SetPosition(140);
  delay(tempo/2);
  servo[0].SetPosition(90);
  servo[1].SetPosition(90);
  delay(tempo/2);

}

void drunk (int tempo){
  
  pause=millis();
  
  int move1[] = {60,70,90,90};
  int move2[] = {110,120,90,90};
  int move3[] = {60,70,90,90};
  int move4[] = {110,120,90,90};
  
  moveNServos(tempo*0.235,move1);
  moveNServos(tempo*0.235,move2);
  moveNServos(tempo*0.235,move3);
  moveNServos(tempo*0.235,move4);
  while(millis()<(pause+tempo));

}


void noGravity(int tempo){
  
  int move1[4] = {120,140,90,90};
  int move2[4] = {140,140,90,90};
  int move3[4] = {120,140,90,90};
  int move4[4] = {90,90,90,90};
  
  
  for(int i=0;i<4;i++) servo[i].SetPosition(90);
  for(int i=0;i<N_SERVOS;i++) oldPosition[i]=90;
  moveNServos(tempo*2,move1);
  moveNServos(tempo*2,move2);
  delay(tempo*2);
  moveNServos(tempo*2,move3);
  moveNServos(tempo*2,move4);

 

}

void kickLeft(int tempo){
  for(int i=0;i<4;i++) servo[i].SetPosition(90);
  delay(tempo);
  servo[0].SetPosition(50); //pie derecho
  servo[1].SetPosition(70); //pie izquiero
  delay(tempo);
  servo[0].SetPosition(80); //pie derecho
  servo[1].SetPosition(70); //pie izquiero
  delay(tempo/4);
  servo[0].SetPosition(30); //pie derecho
  servo[1].SetPosition(70); //pie izquiero
  delay(tempo/4);
  servo[0].SetPosition(80); //pie derecho
  servo[1].SetPosition(70); //pie izquiero
  delay(tempo/4);
  servo[0].SetPosition(30); //pie derecho
  servo[1].SetPosition(70); //pie izquiero
  delay(tempo/4);
  servo[0].SetPosition(80); //pie derecho
  servo[1].SetPosition(70); //pie izquiero
  delay(tempo);
}

void kickRight(int tempo){
for(int i=0;i<4;i++) servo[i].SetPosition(90);
  delay(tempo);
  servo[0].SetPosition(110); //pie derecho
  servo[1].SetPosition(130); //pie izquiero
  delay(tempo);
  servo[0].SetPosition(110); //pie derecho
  servo[1].SetPosition(100); //pie izquiero
  delay(tempo/4);
  servo[0].SetPosition(110); //pie derecho
  servo[1].SetPosition(150); //pie izquiero
  delay(tempo/4);
  servo[0].SetPosition(110); //pie derecho
  servo[1].SetPosition(80); //pie izquiero
  delay(tempo/4);
  servo[0].SetPosition(110); //pie derecho
  servo[1].SetPosition(150); //pie izquiero
  delay(tempo/4);
  servo[0].SetPosition(110); //pie derecho
  servo[1].SetPosition(100); //pie izquiero
  delay(tempo);
}

void walk(int steps, int T){
    int A[4]= {15, 15, 30, 30};
    int O[4] = {0, 0, 0, 0};
    double phase_diff[4] = {DEG2RAD(0), DEG2RAD(0), DEG2RAD(90), DEG2RAD(90)};
    
    for(int i=0;i<steps;i++)oscillate(A,O, T, phase_diff);
}

void run(int steps, int T){
    int A[4]= {10, 10, 10, 10};
    int O[4] = {0, 0, 0, 0};
    double phase_diff[4] = {DEG2RAD(0), DEG2RAD(0), DEG2RAD(90), DEG2RAD(90)}; 
    
    for(int i=0;i<steps;i++)oscillate(A,O, T, phase_diff);
}

void backyard(int steps, int T){
    int A[4]= {15, 15, 30, 30};
    int O[4] = {0, 0, 0, 0};
    double phase_diff[4] = {DEG2RAD(0), DEG2RAD(0), DEG2RAD(-90), DEG2RAD(-90)}; 
    
    for(int i=0;i<steps;i++)oscillate(A,O, T, phase_diff);
}

void backyardSlow(int steps, int T){
    int A[4]= {15, 15, 30, 30};
    int O[4] = {0, 0, 0, 0};
    double phase_diff[4] = {DEG2RAD(0), DEG2RAD(0), DEG2RAD(-90), DEG2RAD(-90)}; 
    
    for(int i=0;i<steps;i++)oscillate(A,O, T, phase_diff);
}


void turnLeft(int steps, int T){
    int A[4]= {20, 20, 10, 30};
    int O[4] = {0, 0, 0, 0};
    double phase_diff[4] = {DEG2RAD(0), DEG2RAD(0), DEG2RAD(90), DEG2RAD(90)}; 
    
    for(int i=0;i<steps;i++)oscillate(A,O, T, phase_diff);
}

void turnRight(int steps, int T){
    int A[4]= {20, 20, 30, 10};
    int O[4] = {0, 0, 0, 0};
    double phase_diff[4] = {DEG2RAD(0), DEG2RAD(0), DEG2RAD(90), DEG2RAD(90)}; 
    
    for(int i=0;i<steps;i++)oscillate(A,O, T, phase_diff);
}

void moonWalkRight(int steps, int T){
    int A[4]= {25, 25, 0, 0};
    int O[4] = {-15 ,15, 0, 0};
    double phase_diff[4] = {DEG2RAD(0), DEG2RAD(180 + 120), DEG2RAD(90), DEG2RAD(90)}; 
    
    for(int i=0;i<steps;i++)oscillate(A,O, T, phase_diff);
}

void moonWalkLeft(int steps, int T){
    int A[4]= {25, 25, 0, 0};
    int O[4] = {-15, 15, 0, 0};
    double phase_diff[4] = {DEG2RAD(0), DEG2RAD(180 - 120), DEG2RAD(90), DEG2RAD(90)}; 
    
    for(int i=0;i<steps;i++)oscillate(A,O, T, phase_diff);
}

void crusaito(int steps, int T){
    int A[4]= {25, 25, 30, 30};
    int O[4] = {- 15, 15, 0, 0};
    double phase_diff[4] = {DEG2RAD(0), DEG2RAD(180 + 120), DEG2RAD(90), DEG2RAD(90)}; 
    
    for(int i=0;i<steps;i++)oscillate(A,O, T, phase_diff);
}

void swing(int steps, int T){
    int A[4]= {25, 25, 0, 0};
    int O[4] = {-15, 15, 0, 0};
    double phase_diff[4] = {DEG2RAD(0), DEG2RAD(0), DEG2RAD(90), DEG2RAD(90)};
    
    for(int i=0;i<steps;i++)oscillate(A,O, T, phase_diff);
}

void upDown(int steps, int T){
    int A[4]= {25, 25, 0, 0};
    int O[4] = {-15, 15, 0, 0};
    double phase_diff[4] = {DEG2RAD(180), DEG2RAD(0), DEG2RAD(270), DEG2RAD(270)};
    
    for(int i=0;i<steps;i++)oscillate(A,O, T, phase_diff);
}

void flapping(int steps, int T){
    int A[4]= {15, 15, 8, 8};
    int O[4] = {-A[0], A[1], 0, 0};
    double phase_diff[4] = {DEG2RAD(0), DEG2RAD(180), DEG2RAD(90), DEG2RAD(-90)};
    
    for(int i=0;i<steps;i++)oscillate(A,O, T, phase_diff);
}

void test(int steps, int T){
    int A[4]= {15, 15, 8, 8};
    int O[4] = {-A[0] + 10, A[1] - 10, 0, 0};
    double phase_diff[4] = {DEG2RAD(0), DEG2RAD(180), DEG2RAD(90), DEG2RAD(-90)};
    
    for(int i=0;i<steps;i++)oscillate(A,O, T, phase_diff);
}

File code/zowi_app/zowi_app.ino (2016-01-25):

//----------------------------------------------------------------
//-- Zowi basic firmware v2 (Modded for Zowi community edition)
//-- (c) BQ. Released under a GPL licencse
//-- 25 January 2016
//-- Authors:  Javier Isabel:  javier.isabel@bq.com
//--           Anita de Prado: ana.deprado@bq.com
//--           Jose Alberca:   jose.alberca@bq.com
//--           Juan Gonzalez (obijuan): juan.gonzalez@bq.com
//--           Irene Sanz : irene.sanz@bq.com
//-----------------------------------------------------------------
//-- Experiment with all the features that Zowi have!
//-----------------------------------------------------------------

//-- Library to manage external interruptions

//-- Library to manage serial commands
#include <ZowiSerialCommand.h>
ZowiSerialCommand SCmd;  //The SerialCommand object

//-- Zowi Library
#include <Zowi.h>
Zowi zowi;  //This is Zowi!!
 
//---------------------------------------------------------
//-- Configuration of pins where the servos are attached
/*
         --------------- 
        |               |
        |     O   O     |
        |               |
 YR ==> |               | <== YL
         --------------- 
            ||     ||
            ||     ||
            ||     ||
 RR ==>  ------   ------  <== RL
         ------   ------
*/

  #define PIN_YL 2 //servo[0]
  #define PIN_YR 3 //servo[1]
  #define PIN_RL 4 //servo[2]
  #define PIN_RR 5 //servo[3]
//---------------------------------------------------------

///////////////////////////////////////////////////////////////////
//-- Global Variables -------------------------------------------//
///////////////////////////////////////////////////////////////////

const char programID[]="ZOWI_BASE_v2"; //Each program will have a ID

const char name_fac='$'; //Factory name
const char name_fir='#'; //First name

//-- Movement parameters
int T=1000;              //Initial duration of movement
int moveId=0;            //Number of movement
int moveSize=15;         //Asociated with the height of some movements

//---------------------------------------------------------
//-- Zowi has 5 modes:
//--    * MODE = 0: Zowi is awaiting  
//--    * MODE = 1: Dancing mode!  
//--    * MODE = 2: Obstacle detector mode  
//--    * MODE = 3: Noise detector mode   
//--    * MODE = 4: ZowiPAD or any Teleoperation mode (listening SerialPort). 
//--
volatile int MODE=0; //State of zowi in the principal state machine. 
//--------------------------------------------------------- 

unsigned long previousMillis=0;

int randomDance=0;
int randomSteps=0;

bool obstacleDetected = false;


///////////////////////////////////////////////////////////////////
//-- Setup ------------------------------------------------------//
///////////////////////////////////////////////////////////////////
void setup(){

  //Serial communication initialization
  Serial.begin(19200);  

  //Set the servo pins
  zowi.init(PIN_YL,PIN_YR,PIN_RL,PIN_RR,true);
 
  //Uncomment this to set the servo trims manually and save on EEPROM 
    //zowi.setTrims(TRIM_YL, TRIM_YR, TRIM_RL, TRIM_RR);
    //zowi.saveTrimsOnEEPROM(); //Uncomment this only for one upload when you finaly set the trims.

  //Set a random seed
  randomSeed(analogRead(A6));

  //Setup callbacks for SerialCommand commands 
  SCmd.addCommand("S", receiveStop);      //  sendAck & sendFinalAck
  //SCmd.addCommand("L", receiveLED);       //  sendAck & sendFinalAck
  SCmd.addCommand("T", recieveBuzzer);    //  sendAck & sendFinalAck
  SCmd.addCommand("M", receiveMovement);  //  sendAck & sendFinalAck
  SCmd.addCommand("H", receiveGesture);   //  sendAck & sendFinalAck
  SCmd.addCommand("K", receiveSing);      //  sendAck & sendFinalAck
  SCmd.addCommand("C", receiveTrims);     //  sendAck & sendFinalAck
  SCmd.addCommand("G", receiveServo);     //  sendAck & sendFinalAck
  SCmd.addCommand("R", receiveName);      //  sendAck & sendFinalAck
  SCmd.addCommand("E", requestName);
  SCmd.addCommand("D", requestDistance);
  SCmd.addCommand("N", requestNoise);
  //SCmd.addCommand("B", requestBattery);
  SCmd.addCommand("I", requestProgramId);
  SCmd.addDefaultHandler(receiveStop);



  //Zowi wake up!
  zowi.sing(S_connection);
  zowi.home();


  //If Zowi's name is '&' (factory name) means that is the first time this program is executed.
  //This first time, Zowi mustn't do anything. Just born at the factory!
  //5 = EEPROM address that contains first name character
  /*if (EEPROM.read(5)==name_fac){ 

    EEPROM.put(5, name_fir); //From now, the name is '#'
    EEPROM.put(6, '\0'); 

    while(true){    
       delay(1000);
    }
  }*/  


  //Send Zowi name, programID & battery level.
  requestName();

  //Smile for a happy Zowi :)
    zowi.sing(S_happy);
    delay(200);
  


  //If Zowi's name is '#' means that Zowi hasn't been baptized
  //In this case, Zowi does a longer greeting
  //5 = EEPROM address that contains first name character
  if (EEPROM.read(5)==name_fir){ 

  previousMillis = millis();
  }
}



///////////////////////////////////////////////////////////////////
//-- Principal Loop ---------------------------------------------//
///////////////////////////////////////////////////////////////////
void loop() {


  if (Serial.available()>0 && MODE!=4){
    MODE=4;
  }
  else{

    switch (MODE) {

      //-- MODE 0 - Zowi is awaiting
      //---------------------------------------------------------
      case 0:
      
        //Every 80 seconds in this mode, Zowi falls asleep 
        if (millis()-previousMillis>=80000){
            ZowiSleeping_withInterrupts(); //ZZzzzzz...
            previousMillis=millis();         
        }

        break;
      

      //-- MODE 4 - ZowiPAD or any Teleoperation mode (listening SerialPort) 
      //---------------------------------------------------------
      case 4:

        SCmd.readSerial();
        
        //If Zowi is moving yet
        if (zowi.getRestState()==false){  
          move(moveId);
        }
      
        break;      


      default:
          MODE=4;
          break;
    }

  } 

}  

//-- Function to receive Stop command.
void receiveStop(){

    sendAck();
    zowi.home();
    sendFinalAck();

}

//-- Function to receive buzzer commands
void recieveBuzzer(){
  
    //sendAck & stop if necessary
    sendAck();
    zowi.home(); 

    bool error = false; 
    int frec;
    int duration; 
    char *arg; 
    
    arg = SCmd.next(); 
    if (arg != NULL) { frec=atoi(arg); }    // Converts a char string to an integer   
    else {error=true;}
    
    arg = SCmd.next(); 
    if (arg != NULL) { duration=atoi(arg); } // Converts a char string to an integer  
    else {error=true;}

    if(error==true){

      delay(2000);

    }else{ 

      zowi._tone(frec, duration, 1);   
    }

    sendFinalAck();

}
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

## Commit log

2015-02-17 Added 3D models (step,stl,freecad)
    [body.step, body.stl, chassis.step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]
2015-02-17 Test 1 with oscillators. It walks pretty well
    [Oscillator_test1.ino]
2015-02-18 New gaits with oscillators (Ardusnake library)
    [Oscillator_test1.ino]
2015-02-18 Oscillators: More gaits added
    [Oscillator_test1.ino]
2015-02-18 Bug fixed in the moving forward gait
    [Oscillator_test1.ino]
2015-02-18 Oscillators: Code cleaned a little bit
    [Oscillator_test1.ino]
2015-02-23 Fixed bad design on legs
    [body.step, leg.step, leg.stl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]
2015-03-04 Solved some small issues on printable parts
    [body.step, body.stl, chassis.step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]
2015-03-06 Bigger room on chassis for the battery
    [chassis.step, chassis.stl, zob.fcstd]
2015-03-20 Updated freecad model and remote swing program
    [zob.fcstd]
2015-03-27 Updated FreeCAD project with deep mods for a better assembly experience
2015-03-30 Updated stl and step files
    [body.step, body.stl, chassis.step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]
2015-04-12 Scopum version by HackLab UPM Bq
    [ZUM_BT_328.stl, arm_part1.step, arm_part1.stl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]
2015-04-12 Revert "Scopum version by HackLab UPM Bq"
    This reverts commit e950cbce4d960e393f1a8efa93e7bc7a20ef1a0e.
    [ZUM_BT_328.stl, arm_part1.step, arm_part1.stl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]
2015-04-17 Fixed a bad design on chassis part
    [chassis.step, chassis.stl]
2015-04-27 Fixed code for Arduino IDE version > 1.5
    [smooth_criminal.ino]
2015-04-28 Modified chassis
    [chassis.step, chassis.stl]
2015-05-27 updated step files
    [body.step, chassis.step, footL.step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]
2015-06-02 Calibration code, with instructions
2015-06-02 fixed error in calibration code
    [calibration.ino]
2015-07-08 Modified head and chassis for an easier assembly
    [body.stl, chassis.stl]
2015-07-22 Leg part refactored. Implemented using sketches instead of booleans operations
2015-07-23 fake ultrasound added. It is for printing it instead of installing the real sensor (just in case you do not have one)
2015-07-28 Some test with oscillator-test1
    [Oscillator_test1.ino]
2015-07-29 Full assembly and Bill of materials added to the freecad file
2015-07-29 zowi BOM added (images and text) in README
2016-02-03 Added 3d model of ZORRAIDER
    [armL.stl, armR.stl, body.stl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]
2016-02-03 directory refactor
    [armL.stl, armR.stl, body.stl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]
2016-02-05 Forge mod added
    [armL.stl, armR.stl, body.stl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]
2016-02-08 Bigger hands for zorraider
    [handL.stl, handR.stl]
2016-02-09 Añadido Zowiquilator
    [Base_fixed.stl, BrazoD_fixed.stl, BrazoI_fixed.stl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]
2016-02-15 Update zowiquilator.cpp
    renamed PIN/TRIM to make installing easier
2016-02-15 Update zowiquilator.cpp
    fixed spelling error
    [zowiquilator.cpp]
2016-02-16 Added kobuki parts
    [CABEZA.stl, CUELLO.stl, HUMERO.stl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]
2016-02-16 new filename
    [HUMERO.stl, head.stl, humerus right.stl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]
2016-02-16 add base.stl
    [base.stl]
2016-02-18 generated stl, step, and obj files
    [body.step, body.stl, chassis.step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]
2016-02-23 solved bug in walk function
    [remote_control.cpp]
2016-02-24 fixed micro raider code
    [remote_control.cpp]
2016-02-24 re-generated obj, step, stl files
    [leftArm.step, leftArm.stl, rightArm.step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]
2016-02-25 Added IronZowi mod
    [arms.stl, base.stl, ear1.stl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]
2016-02-26 uploaded PunoD_fixed
    [PunoD_fixed.stl, punoi_fixed.stl]
2016-02-26 Foot and Head fixed (zowarrior)
    [FootLeft.SLDPRT, FootLeft.STL, medieval.SLDPRT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]
